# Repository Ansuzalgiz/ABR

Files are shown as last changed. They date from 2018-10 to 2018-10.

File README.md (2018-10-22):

# Project ABR

The ABR is an Automatic Bullpup Rifle for Nerf. With simplicity as the main design goal, it uses only 11 printed parts. 

# Features
- Simple design: only 11 printed parts
- Dual stage trigger
- 42mm flywheel gap
- Full length dart feed guide
- Kuryaka's automatic pusher

# Required Parts

|Part |Quantity  |Description |
|---|---|---|
|Flywheel motors |2 |130 or 180 sized motors for flywheels |
|Flywheels |2 |Flywheels |
|Pusher motor |1 |130 sized motor for pusher (180 might work) 
|Worm gear |1 |For pusher - [Amazon link](https://www.amazon.com/gp/product/B00EPQMKHQ/ref=oh_aui_detailpage_o09_s00) |
|Heat set threaded inserts| 13 | To hold in screws (McMaster 94180A333 for 100) |
|Compression Spring | 1 | For trigger (McMaster 9657K56 for 12) |
|Torsion Spring | 1 | For magazine release (McMaster 9271K579 for 6) |
|M3x10 Socket head screws | 9 | |
|M3x14 Socket head screw  | 1 | Used as axle for pusher assembly |
|M3x25 Socket head screws | 2 | Used for flywheel switch and trigger |
|M3x35 Socket head screw  | 1 | For magazine release |
|M2 screws | 5 | For motors |

# Printing Parameters
Prototypes were printed using these parameters:
- PLA
- .2mm layer height
- .4mm nozzle
- No supports

# Assembly

[Assembly log on Imgur](https://imgur.com/a/5xSceZQ)

# Purchasing 3D Printed Parts

I sell the [latest revision of the 3D printed parts on Etsy](https://www.etsy.com/listing/634103494/nerf-abr-3d-printed-parts-kit).

# Issues
## Jams when using cheap Lightake 12rd Nerf magazines
I think this is due to the magazine not feeding darts fast enough. It might also be due to the tight magazine well squeezing the magazine. 

# TODO
## BOOMco. conversion
Add alternate barrel to adapt blaster to use BOOMco. darts using [Boomtendo's Nerf->BOOMco. magazine feed lip](https://www.thingiverse.com/thing:2853522). 

## OpenFlywheelProject Eclipse compatability
Add alternate barrel and flywheel motor mount of OFP Eclipse flywheels

## Document proper assembly instructions
Create some nicer assembly instructions than a imgur gallery. 

# Contributing
The project was designed using Fusion 360, under their hobbyist license. Upon updating or adding a part, export and override the changed part STEP and STLs.

# Attributions
This project uses the [Nerf Automatic Pusher by Kuryaka](https://www.thingiverse.com/thing:2980651)

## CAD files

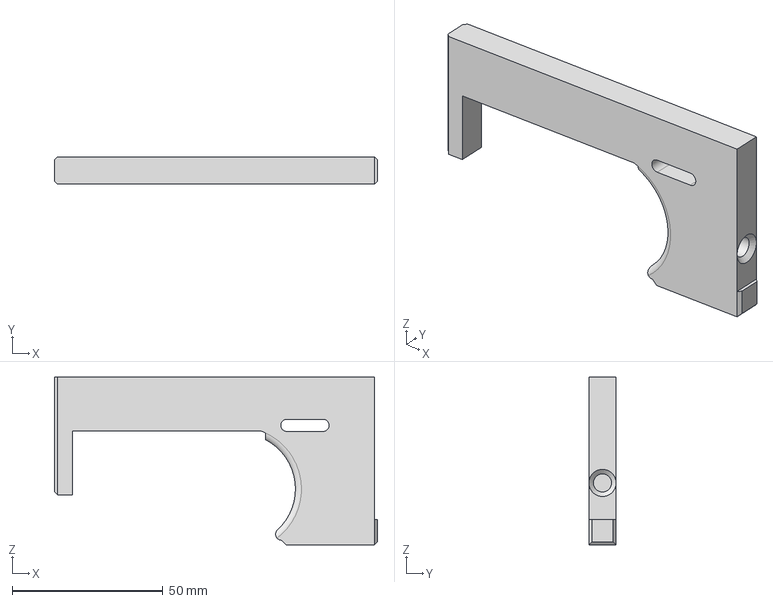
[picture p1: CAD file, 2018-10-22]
STEP/Trigger.step
107.0 x 9.00 x 55.5 mm

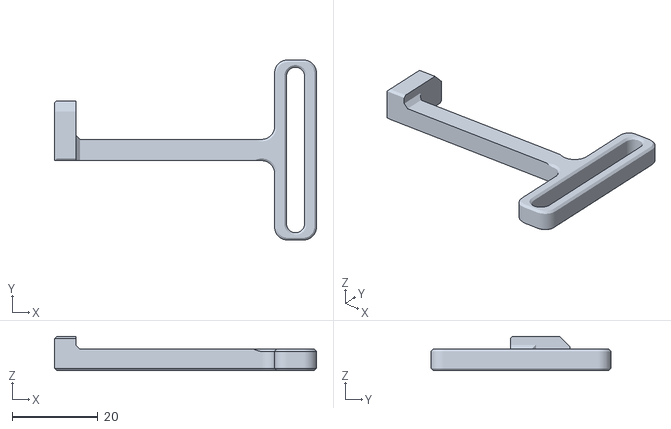
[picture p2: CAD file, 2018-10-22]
STLs/Pusher1_Mini.stl
61.3 x 42.1 x 8.00

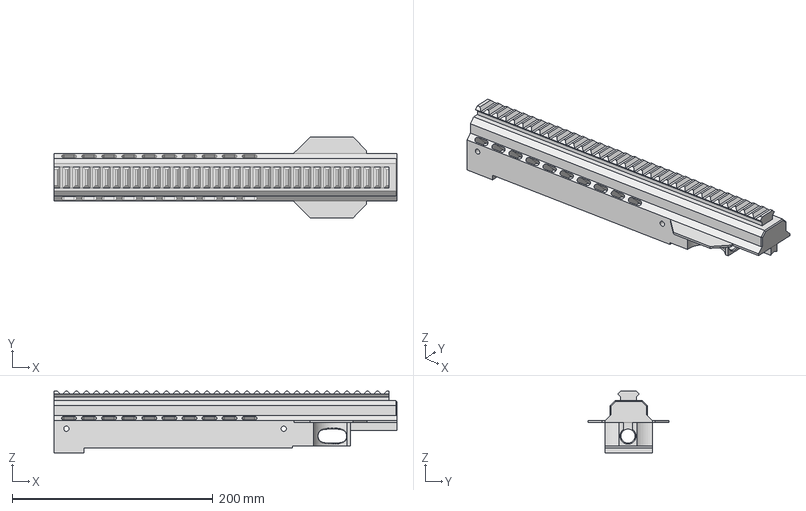
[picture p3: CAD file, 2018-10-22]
STEP/Barrel.step
342.0 x 80.6 x 61.4 mm

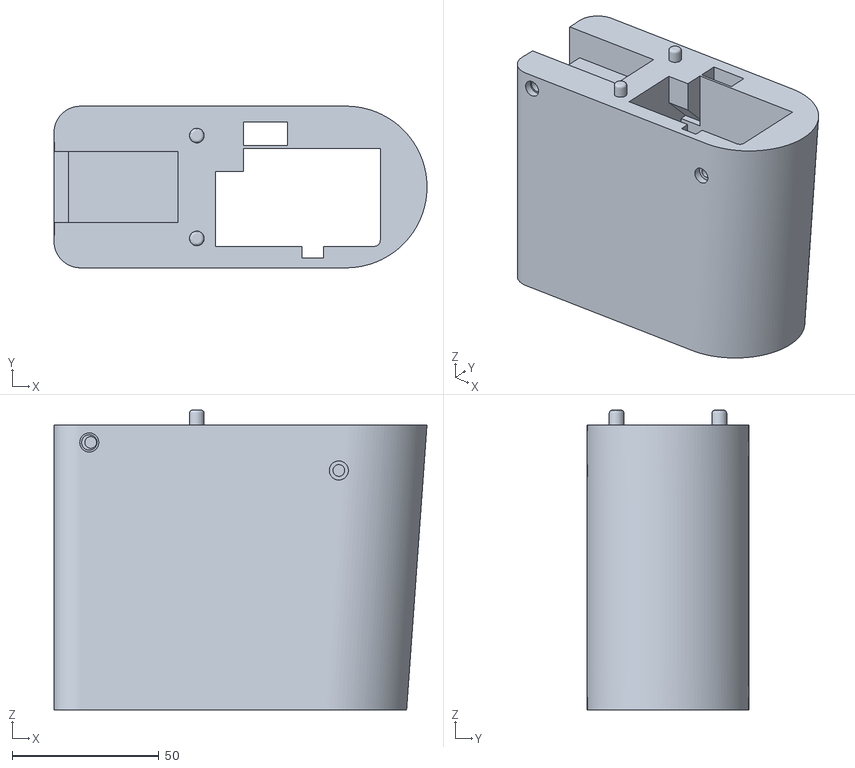
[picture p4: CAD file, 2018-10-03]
STLs/Shell-CR-10-Rear.stl
126.9 x 55.0 x 102.0

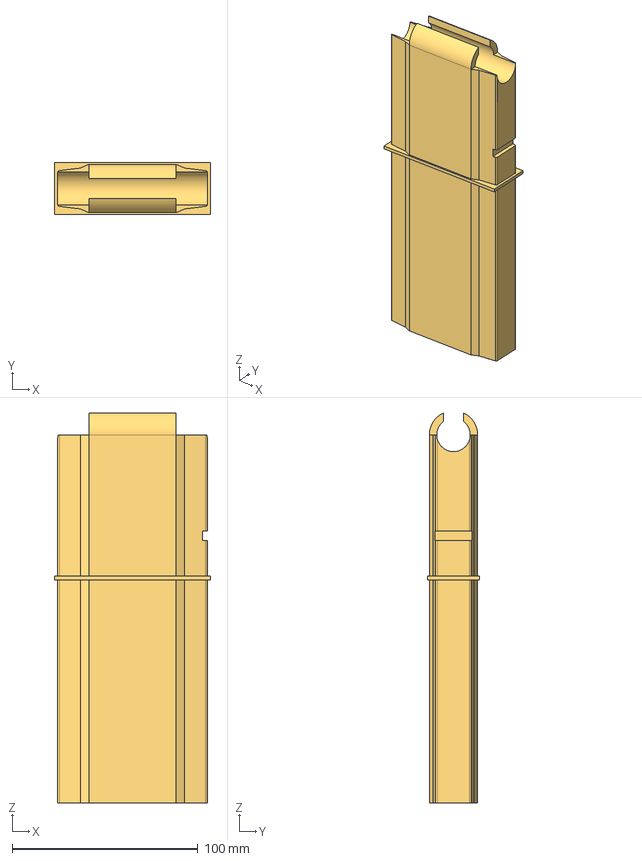
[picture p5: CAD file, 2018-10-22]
STEP/NerfMagazine.step
84.0 x 28.0 x 209.8 mm

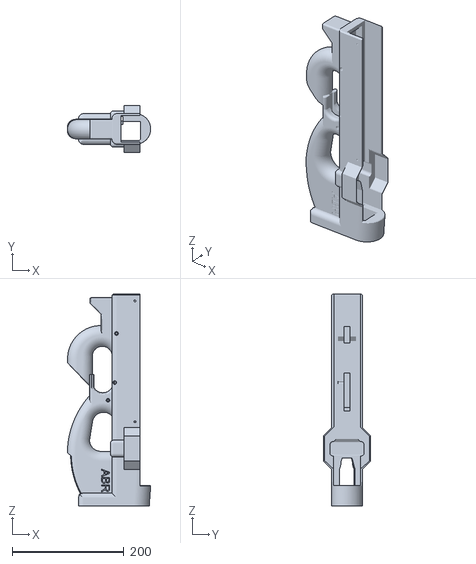
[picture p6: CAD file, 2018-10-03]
STLs/Shell-CR-10-Front.stl
149.5 x 85.0 x 380.0

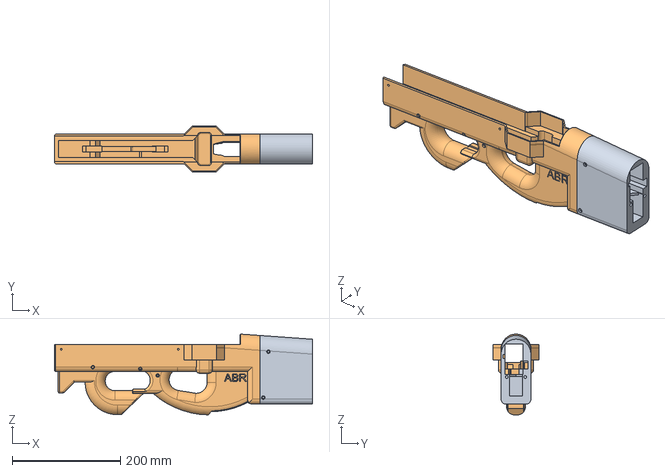
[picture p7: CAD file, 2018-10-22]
STEP/SplitShell.step
477.0 x 85.0 x 149.5 mm

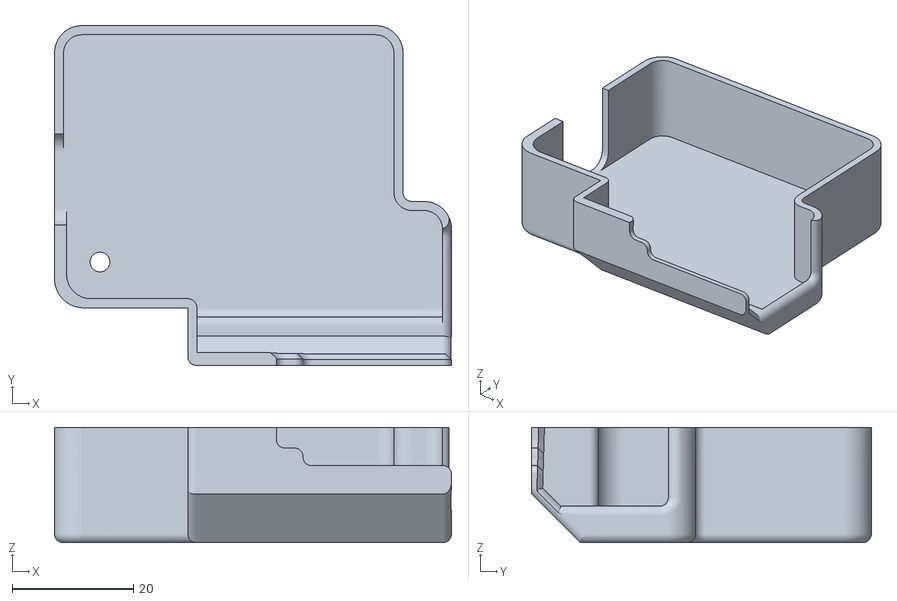
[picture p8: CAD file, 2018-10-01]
STLs/BoxCover_Direct40R.stl
65.5 x 56.0 x 19.0

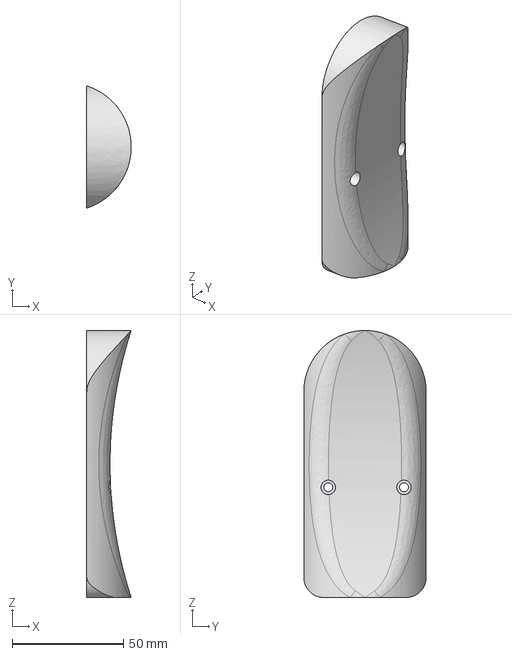
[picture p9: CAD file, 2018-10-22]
STEP/StockPlate.step
20.0 x 55.0 x 120.0 mm

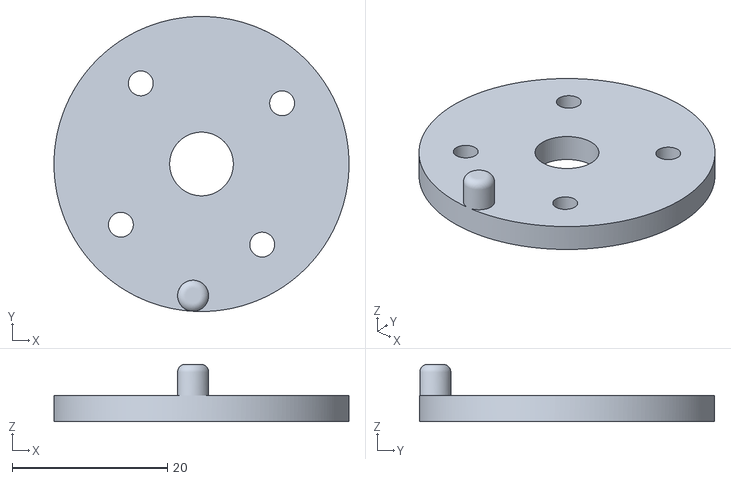
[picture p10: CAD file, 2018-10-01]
STLs/40GearSpacer.stl
38.0 x 38.0 x 7.40

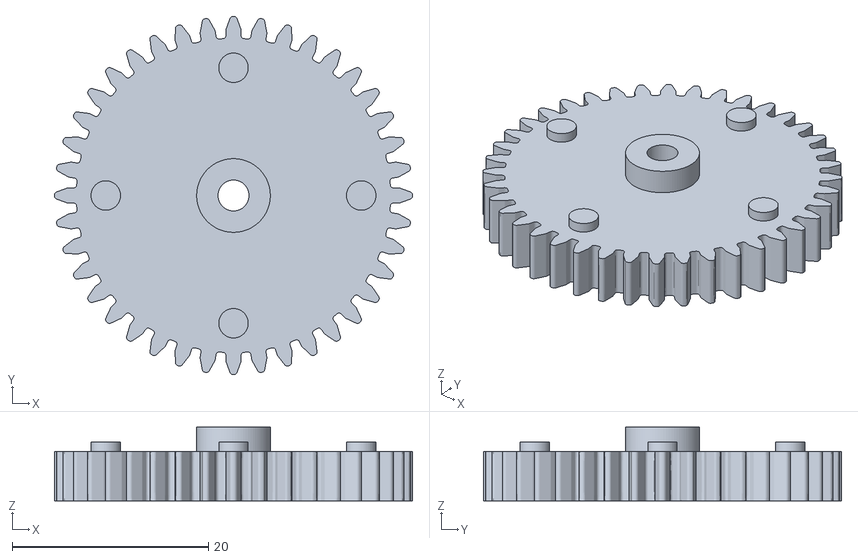
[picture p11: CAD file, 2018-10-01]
STLs/40Gear.stl
36.4 x 36.4 x 7.50

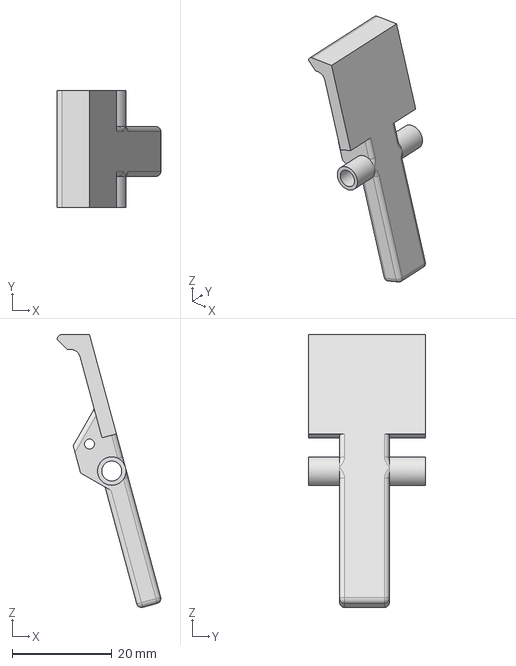
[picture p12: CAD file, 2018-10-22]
STEP/MagRelease.step
20.8 x 23.5 x 54.8 mm

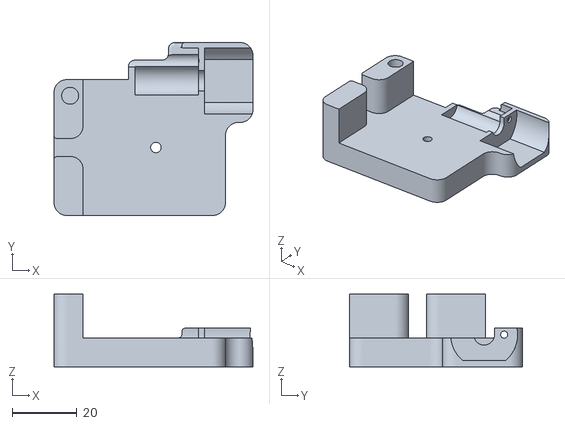
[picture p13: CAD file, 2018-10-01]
STLs/DirectBoxBottom40_Rotate.stl
61.5 x 53.4 x 22.5

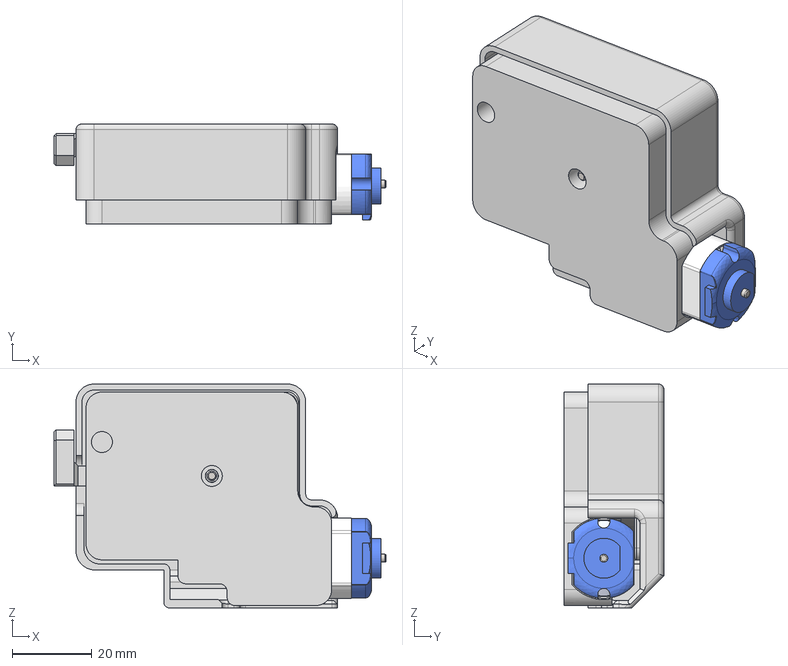
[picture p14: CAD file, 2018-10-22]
STEP/Pusher.step
83.1 x 25.0 x 56.0 mm
Pusher1_Mini
DirectBoxBottom40_Rotate
40Gear
40GearSpacer
simpler130
Axle
BoxCover_Direct40R

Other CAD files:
STEP/Shell.step
STEP/FlywheelCage.step
STLs/Barrel.stl
STLs/FlywheelCage.stl
STLs/MagRelease.stl
STLs/Shell.stl
STLs/StockPlate.stl
STLs/Trigger.stl

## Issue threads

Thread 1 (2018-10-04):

More part links?

jchristman, 2018-10-04:
I’m relatively new to print engineering. Would you mind dropping some more links to parts you use? Particularly a supplier for the M screws, and links to the various flywheels/motors would be really helpful.

Thanks! Awesome design!! Excited to print one off to keep at my desk at work (we regularly have nerf wars).

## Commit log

2018-10-01 Upload project files
    [40Gear.stl, 40GearSpacer.stl, ABR.f3d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]
2018-10-03 Added shell cut for CR-10
    Cut shell into 380 and 100mm segments for CR-10 owners.
    [ABR.f3d, ABR.step, Shell-CR-10-Front.stl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]
2018-10-05 Fixed Magazine Release interfering with 12/18 round Hasbro magazines
    [ABR.f3d, ABR.step, MagRelease.stl]
2018-10-05 Improved FlywheelCage tolerances
    [ABR.f3d, ABR.step, FlywheelCage.stl]
2018-10-06 Updated FlywheelCage for better printability
    [ABR.f3d, ABR.step, FlywheelCage.stl]
2018-10-22 Reorganized project
    Exported parts out as separate STEP files to allow each to be versioned
    separately. Also makes it easier to add variations to the project, like
    the ABR-2 and ABR-2^2
    [ABR.f3d, ABR.step, Barrel.step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]
